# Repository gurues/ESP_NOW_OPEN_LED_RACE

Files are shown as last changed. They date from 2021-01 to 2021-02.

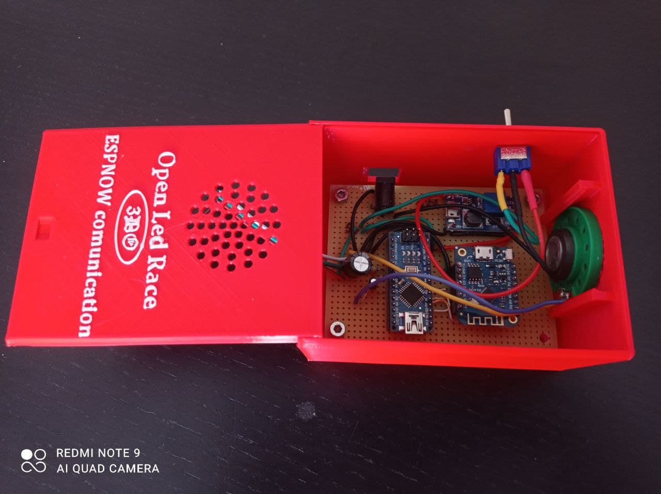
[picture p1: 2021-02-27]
Desing-3D/Fotos/Control_Box_7.jpg

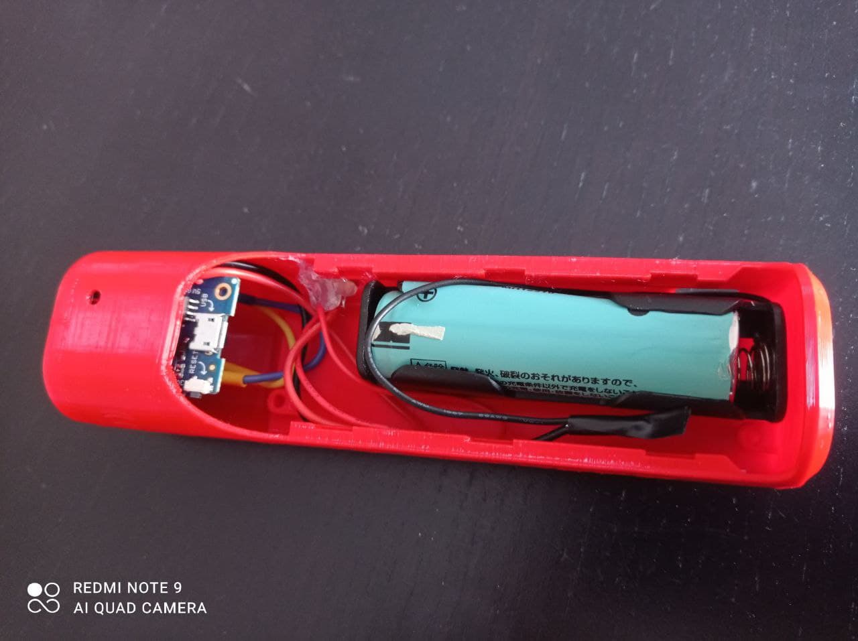
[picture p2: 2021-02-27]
Desing-3D/Fotos/OLR_Mando_Interior_4.jpg

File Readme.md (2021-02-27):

## -----------------------------------------------------------------------------------------------------------

# OPEN LED RACE ESPNOW COMUNICATION (4 PLAYER)

## ------------------------------------------------------------------------------------------------------------

### Cuando era pequeño siempre pedía para reyes un scalextri, pero los reyes pensaban en otros regalos mejores para mí

### Desde que vi el proyecto Open Led Race (https://openledrace.net/) sabía que lo construiría para mis hijos ... y para mí. Después ví un proyecto de Germán Martín realizando mandos inalámbricos mediante comunicación ESPNOW y ESP8266 (https://github.com/gmag11/OpenLedRace-Wireless-Remote). Investigue un poco sobre este tipo de comunicación (https://randomnerdtutorials.com/esp-now-many-to-one-esp8266-nodemcu/) y la aplique a este proyecto de una forma mucho más fácil y primitiva que Germán

### El resultado es una adaptación del código Open Led Race de 4 player (https://gitlab.com/open-led-race/olr-arduino) donde los mandos son inalámbricos mediante comunicación ESPNOW. He diseñado 2 pequeños códigos uno para los mandos con comunicación ESPNOW y otro para el Gateway ESPNOW

### El funcionamiento es muy básico, cuando se pulsa el pulsador de cualquier mando se produce una interrupción en el propio mando lo que provoca que se envíe un mensaje mediante el protocolo ESPNOW con la siguiente información:

- Número de Jugador
- Dato "0" o "1" (rota de forma cíclica -> 0, 1, 0, 1, 0 .......)
  
### El Gateway recibe todos los mensajes de los mandos enlazados al mismo, y teniendo en cuenta el Jugador y el dato asociado activa o no el puerto correspondiente al jugador en el Open Led Race

### Para que la comunicación entre los mandos y el Gateway ESPNOW sea efectiva es necesario saber la Mac Address del microcontrolador que realizará la función de Gateway, en nuestro caso un Wemos D1 mini. Para determinar la MAC puedes cargar el código que está en la carpeta "MAC_Address" en el Wemos del Gateway (código obtenido de https://randomtutorials.com/)

## MANDO ESPNOW

### El código de los mando con comunicación ESPNOW se encuentra en la carpeta "ESP_NOW_Mando_OLR"

### Para un funcionamiento correcto se debe modificar las siguientes variables:

### // Gateway_ESPNOW MAC Address

### uint8_t broadcastAddress[] = {0x??, 0x??, 0x??, 0x??, 0x??, 0x??};

- Introducir la dirección MAC del Gateway_ESPNOW para emparejar los mandos con el Gateway ESPNOW

### Indica el número del mando del jugador a configurar

### 1 -> Jugador 1   Rojo

### 2 -> Jugador 2   Verde

### 3 -> Jugador 3   Azul

### 4 -> Jugador 4   Blanco

### #define JUGADOR ?

- Introducir el número de jugador para que se configure dicho mando.

## GATEWAY ESPNOW

### El código del Gateway ESPNOW se encuentra en la carpeta "ESP_NOW_Gateway_OLR". No es necesaria la configuración de ninguna variable para su correcto funcionamiento

## OPEN LED RACE

### El código del programa Open Led Race se encuentra en la carpeta "Open_Led_Race_4_Player" y solo se ha modificado respecto al original lo siguiente:

- Aumentar la espera para la configuración de mandos y carrera
  - línea 825:   delay(3000);  // gurues -> Retraso para la configuración

- Configuración de 4 JUGADORES. Solo es necesario pulsar el último mando a configurar
  - linea 834:   controller_init( &switchs[2], DIGITAL_MODE, DIG_CONTROL_3 );  // gurues
  - linea 835:   car_init( &cars[2], &switchs[2], COLOR3 );                    // gurues
  - linea 836:   ++race.numcars;                                               // gurues

- Activación permanente del sonido
  - línea 866:   SMOTOR=1; // gurues -> Activación del sonido motor

### Si lo crees necesario, modifica los parámetros por defecto de la carrera. Se realiza en el archivo olr-param.h cambiando los siguientes parámetros:

- Número de led de la pista
  - línea 13:  #define MAXLED       300

- Número de led de los Boxes
  - línea 14:  #define BOXLEN       60

- Número de vueltas de la carrera
  - línea 15:  #define NUMLAP       5

### El Open Lace Race (4 Players) guarda las configuraciones en la EEPROM del Arduino nano, por lo que es posible que aún modificando el número de led en el programa si la EEPROM se ha actualizado no te actualice el número máximo de led. La modificación de los parámetros de configuración grabados en la EEPROM se pueden modificar mediante comandos por el puerto serie o con la aplicación desarrollada en el proyecto Open Lace Race (App -> https://gitlab.com/open-led-race/desktopapp/-/tree/master/). En la carpeta Desing-3D esta un manual para la configuración del Open Led Race mediante puerto serie en el archivo OLRN_Protocol_Serial.pdf

### La configuración de los jugadores y resto de opciones se mantienen como las del código original (https://openledrace.net/tutorials/), con la salvedad que para obtener un "0" o un "1" cuando se pulsa el mando es necesario observa el led del Wemos Gateway ESPNOW. Si el led está encendido el dato recibido es un "0" si está apagado el dato recibido es un "1". También cabe la posibilidad de añadir un led externo para verficar esta indicación conectándolo a la patilla D4 del Wemos Gateway ESPNOW, a través de una  resistencia de 220 ohmios. La modificación de los parámetros de configuración se ejecuta durante el proceso de arranque, cuando el dato recibido del mando correspondiente es un "0", igual que en el código original del Open Led Race. La única diferencia respecto a las configuraciones en el momento de arranque es que solo es necesario pulsar sobre el último mando a utilizar. Si quieres configurar para 3 Players, se pulsará el mando del Jugador 3 y si quieres configurar para 4 Players, se pulsará solo el mando del jugador 4

## INTERCONEXIÓN ENTRE OPEN LED RACE y GATEWAY ESPNOW / CONEXIONES MANDO ESPNOW OLR

### La conexión entre el Gateway ESPNOW y el Arduino Nano se realiza puerto a puerto: (WEMOS D1, D2, D3, D5) -> Arduino Nano (A2, A0, A3, A1)

### Las tiras de led pueden ser alimentadas a 5V o a 12V, por lo que en el diseño de las conexiones se incluye un interruptor para seleccionar la alimentación del proyecto, y de esta forma utilizar ambas tiras de led

### En la carpeta "Desing-3D" encontraras un esquema eléctrico de las conexiones realizadas así como su diseño PCB (El PCB no ha sido probado, por lo que no garantizo su funcionamiento). También encontraras una colección de fotos del proyecto

## CONEXIONES MANDO ESPNOW OLR

### Los mandos OLR ESPNOW se pueden realizar de tres formas diferentes:

- 1ª OPCIÓN: Mediante un porta baterias 18650 con cargador y protecciones inclidas en el "shield", botón pulsador y Wemos D1 mini.
- 2ª OPCIÓN: Mediante porta baterias 18650, modulo de carga y protecciones de baterias 18650 TP4056, microinterruptor de 2 polos, botón pulsador y Wemos D1 mini.
- 3ª OPCIÓN: Mediante botón puldador, "shield" porta baterias 18650, cargador y protecciones ademas de el WEMOS D1 mini o ESP32, todo en la misma placa. Esta opción es la más facil de montar y la más económica.

### En la carpeta "Desing-3D" encontraras fotos de las conexiones de los mandos OLR ESPNOW

## DISEÑOS 3D

### En la carpeta "Desing-3D" se encuentran los diseños 3D de los mandos ESPNOW, caja de control, soportes para los mandos y la caja de control así como soportes para la tira led

### El diseño de los mandos es de German Martín, con unas pequeñas modificaciones mias para ajustar dicho diseño a los componentes utilizados en este proyecto (Gracias Germán por compartir los diseños)

## MATERIAL NECESARIO

### Mandos y Gateway ESPNOW

- 5 Wemos D1 mini (4 mandos y el Gateway ESPNOW) (4,25 €) -> https://es.aliexpress.com/item/32529101036.html?spm=a2g0s.9042311.0.0.36f663c0WOJN3M
- 4 Pulsadores (5,69€) -> https://es.aliexpress.com/item/32858643564.html?spm=a2g0s.9042311.0.0.274263c0AGlmOz
- 4 Cargadores Batería 18650 (2,74€) -> https://es.aliexpress.com/item/32910602118.html?spm=a2g0s.9042311.0.0.274263c0Vn9AQd
- 4 WeMos D1 ESP-Wroom-02 ESP8266 Nodemcu con carga de batería 18650 (5,30 €) -> https://es.aliexpress.com/item/4000593916138.html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,scm-url:1007.13339.169870.0,pvid:7de114b2-5daf-4faa-872d-e3b3c1729299,tpp_buckets:668%230%23131923%2363_668%23888%233325%236_668%232846%238113%231998_668%232717%237561%23318_668%231000022185%231000066059%230_668%233468%2315608%23151
  (sustituye a 4 Wemos D1 mini y a los 4 cargadores 18650)
- 4 Wemos ESP-Wroom-32 Bateria-Wifi-Bluetooth (7,14 €) -> https://es.aliexpress.com/item/32819459737.html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,searchweb201602_,searchweb201603_
  (sustituye a 4 Wemos D1 mini y a los 4 cargadores 18650)
- 4 Baterías 18650 (14,95€) -> https://es.aliexpress.com/item/1005001969453906.html?spm=a2g0s.9042311.0.0.274263c08zAvmg
- 1 Adaptador de corriente Booster DC-DC 2A (1,50€) -> https://es.aliexpress.com/item/32952511309.html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,searchweb201602_,searchweb201603_
- 1 Conector de alimentación (2,01€) -> https://es.aliexpress.com/item/33026528272.html?spm=a2g0s.9042311.0.0.274263c0Vn9AQd
- 1 Interruptor de 3 posiciones (1,28€) -> https://es.aliexpress.com/item/32869900104.html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,searchweb201602_,searchweb201603_

### Open Led Race

- Tira de led de 5V o 12V 8112B (13,74 €) -> https://es.aliexpress.com/item/32682015405.html?spm=a2g0s.9042311.0.0.36f663c0WOJN3M
- 1 Ardino Nano Every (12,10 €) -> https://www.amazon.es/Arduino-Nano-Every-Single-Board/dp/B07VX7MX27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
- 1 Resistencia de 470 ohmios (1,64€) -> https://es.aliexpress.com/item/32317115890.html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,searchweb201602_,searchweb201603_
- 2 Condensadores electrolíticos de 1000 microfaradios (2,78€) -> https://es.aliexpress.com/item/32954075821.html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,searchweb201602_,searchweb201603_
- 1 Condensador electrolítico de 1 microfaradio (4,84€) -> https://es.aliexpress.com/item/4000020803391.html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,searchweb201602_,searchweb201603_
- 1 Altavoz 8R 0.25W 40 mm (1,58€) -> https://es.aliexpress.com/item/4001098796204.html?spm=a2g0s.9042311.0.0.274263c0AGlmOz
- Fuente alimentación 5V 3A (4€) -> https://es.aliexpress.com/item/32986101102.html?spm=a2g0s.9042311.0.0.274263c0AGlmOz

## -----------------------------------------------------------------------------------------------------------

# OPEN LED RACE ESPNOW COMUNICATION (2 PLAYER)
## -----------------------------------------------------------------------------------------------------------

### En la carpeta "ESP_NOW_Gateway_OLR_2P" se dispone del código Open Led Race, versión Arduino-Basico (https://gitlab.com/open-led-race/olr-arduino-basic), adaptado para que mediante solo el Gateway ESPNOW poder controlar la tira de led. Resumiendo, eliminando el Arduino Nano y manteniendo el resto de componentes disponenos de un Open Led Race para 2 jugadores (necesario 3 Wemos y el resto de componentes)

### Creo que la versión de 4 player también es posible realizar esta modificación pero es bastante más complicada por lo que ya veré si lo intento más adelante

## -----------------------------------------------------------------------------------------------------------

# PLATFORMIO

## -----------------------------------------------------------------------------------------------------------

### El proyecto está realizado con Platformio y para cargar el código en los respectivos microcontroladores será necesario ejecutar los siguientes instrucciones

### 1.- Abrir un terminar Platformio

### 2.- Desplázate a la carpeta del código que quieras cargar (ESP_NOW_Gateway_OLR, ESP_NOW_Mando_OLR, etc)

### 3.- Ejecuta la siguiente instrucción para cargar el código en un Wemos d1 mini (Gateway ESPNOW o Mando)

            pio run -e d1_mini -t upload 

### 4.- Ejecuta la siguiente instrucción para cargar el código en un ESP32 esp-wroom-32 (Mando)

            pio run -e wemosbat -t upload 

### 5.- Ejecuta la siguiente instrucción para cargar el código en un Arduino Nano (Open Led Race - Pistas máximo 300 led)

            pio run -e nano328 -t upload

### 6.- Ejecuta la siguiente instrucción para cargar el código en un Arduino Nano Every (Open Led Race - Pistas máximo 1500 led)

            pio run -e nano_every -t upload 

### 7.- Si quieres activar el monitor serie, ejecuta a continuación

            pio device monitor -b 115200

## -----------------------------------------------------------------------------------------------------------

# PRESUPUESTO
## -----------------------------------------------------------------------------------------------------------

### Por unos 80€ puedes disponer de un Open Led Race con Arduino Nano Every, tira de led de 5 metros (60 led/metro IP67) y 4 mandos inalámbricos ESPNOW

### Por unos 40€ puedes disponer de un Open Led Race Wemos Gateway ESPNOW, tira de led de 5 metros (60 led/metro IP67) y 2 mandos inalmbricos ESPNOW

## -----------------------------------------------------------------------------------------------------------

# AGRADECIMIENTOS
## -----------------------------------------------------------------------------------------------------------

### Quiero agradecer a los creadores del proyecto Open Led Race su gran trabajo e imaginación para darnos la posibilidad de disfrutar de este proyecto (https://openledrace.net/)

## También quiero agradecer:

- A Germán Martín su paciencia con las preguntas "nóveles" que tuvo el placer de contestarme en los inicios de este proyecto, así como su aportación "al mundo maiker" compartiendo un gran número de proyectos y librerías (https://github.com/gmag11)
- A Rui Santos por sus grandísimos tutoriales de los cuales he aprendido para poder realizar este y otros proyectos (https://randomtutorials.com/)

## gurues@2021

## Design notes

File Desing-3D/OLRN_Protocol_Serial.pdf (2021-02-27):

# OLR Serial Protocol (Board←→Host)

### Table of Contents

Open LED Race - Serial Protocol Ver 1.0 | Pag: 1/24 | Revision: 2020-12-07

## Terminology

In the present doc the terms Board and Host indicate:
- Board: OLR Board - The microcontroller managing the led strip (Arduino)
- Host: A Software running on a computer connected to the Board via Serial interface (Currently only USB).
The software can be “OLR Update/Configuration Utility”, “OpenLEDRace Network Client”, etc.

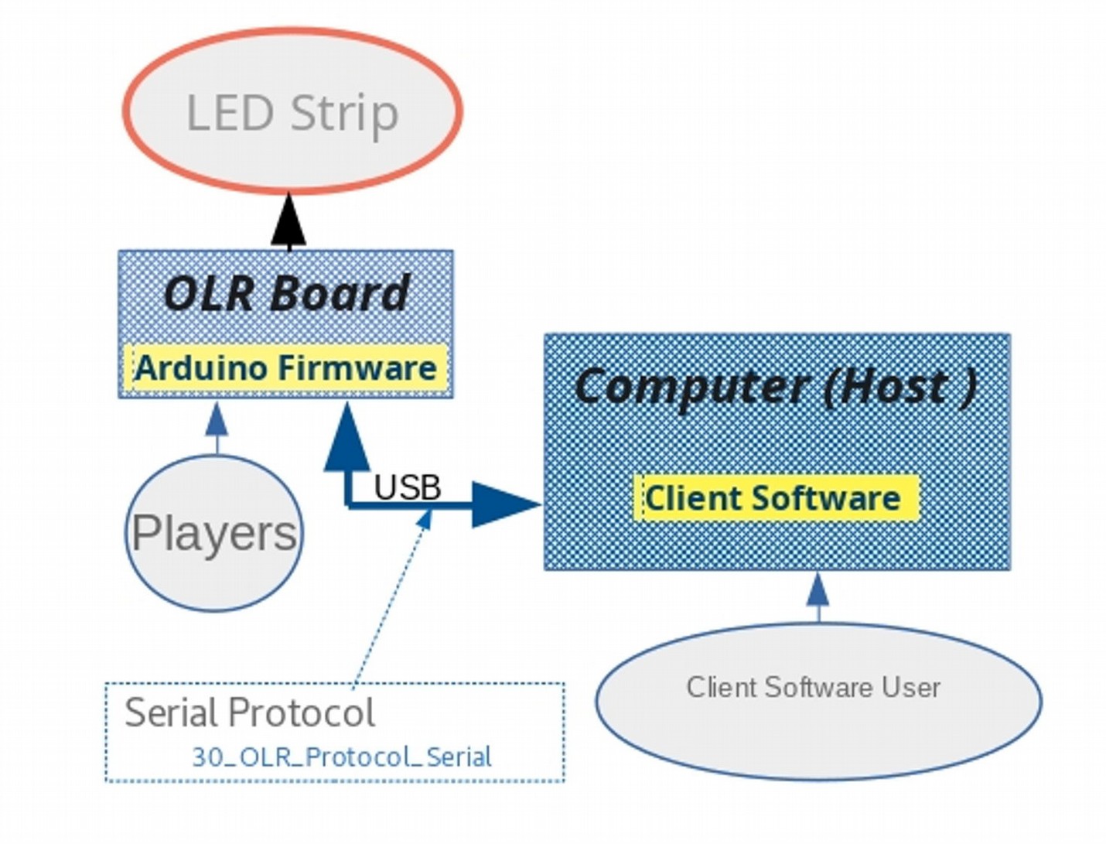
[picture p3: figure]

The software running on Host and the Firmware on Board communicate using the Protocol described in the present document.

## Implementation notes

Message format

Messages are “arrays of chars” composed by:
- Command_id: one char identifying the command, case sensitive
- Optional Parameters (not every command have parameters)
- If a command have parameters, the first one comes immediatly after the command_id (no separators).
- In case command have more than one parameter, the following ones are comma-separated
- EOC - End Of Command char:
- ASCII 10/0x0A = Line Feed = new line = ‘\n’
- Example: C1,3,1,1\n
- Command “C” (race configuration) with parameters, ended with the EOC character
Open LED Race - Serial Protocol Ver 1.0 | Pag: 2/24 | Revision: 2020-12-07

## Commands List

Cmd | | Description | Notes
| # Protocol Handshaking Host-Board handshake on startup
| @ Enter Configuration mode Host request the Board to enter in configuration mode
| ~ Leave Configuration mode Host request the Board to leave configuration mode
| : Set Unique ID Set Board Unique ID
| $ Get UID Get Board Unique Id
| ? Get Software Id (Type) Get Board Software Type (OLR, OLRNet,...) --see specific doc with defined SoftwareType IDs
| % Get Software Version Get Board software version
| ! Send log/error msg Send a log/error message to peer
| C Race Configuration Set main race configuration parameters
| T Track length configuration Command used to configure the Total Number of LEDs in the track.
| B Box length configuration Command used to configure the PitLane (Box)
| A Ramp (Slope) configuration Command used to configure the Ramp (Hill, Slope)
| K Physics parameters configuration Configure “Weight” and “Friction” constants
| H OutTunnel distance notification Set the positions where Board will send the notification for a Car reaching the OutTunnel (The car is ‘n’ position away from the OutTunnel)
| D Load Racetrack defaults Reset to defaults the Racetrack configurable parameters (Track length, Box length, etc)
| W Save current configuration Tell the Board to permamently store current configuration
| Q Query board cfg Host request the current situation of the Config Parameters Set
| R Race phase Command used to notify current Race phase
| p Car current position Telemetry: Car current position in the Racetrack
| r Car Leaving Car is ‘n’ position away from the OutTunnel. The next OLR in the race (the one receiving the car) will receive a ‘Car Coming’ command.
| s Car Left Car is in the last position before OutTunnel. The next OLR in the race will receive a ‘Car Arrived’ command.
| t Car Coming A car is arriving in the OLR (The circuit where it’s now sent a ‘Car Leaving’ command). The Players will see the InTunnel turned on with the color of the arriving car
| u Car Enter A car enter the OLR (The circuit where the car was until now sent a ‘Car Left’ command). The car will ‘come out’ here from the inTunnel.
Open LED Race - Serial Protocol Ver 1.0 | Pag: 3/24 | Revision: 2020-12-07

Cmd | Description | Notes
w Car Win the Race | A car just won the current race

## Commands Description

In the following sections the column “Initiate“ contains the id of the board sending the message.
- B - Board: OLR Board (Arduino Nano)
- H - Host: Host where the OpenLedRace Network Client is running (Computer).
Same rule applies to the “From“ column in “Response“
Some commands may be originated by both peers (ex: Handshake, racephase, etc)
The string [EOC] indicates the EOC (End of Command) char = “line feed” = ASCII 10 (0A)

# protocol handshaking

# | Protocol Handshaking

Initiate | Syntax | Description
B, H | #[EOC] | Sent to initialize a connection (Board and Host)
Response | From | Notes
#[EOC] | H, B | The connection opens succesfully when a “#” is received ‘back’ from the peer

@ Enter Configuration mode

@ | Enter Configuration mode request
initiate | Syntax | Description
H | @[EOC] | Sent from Host to put the board in configuration mode. The OLR Board wil stop managing the current status and wait for configuration commands
Response | From | Notes
@OK[EOC] | B | Board sends “OK” string
@NOK[EOC] | B | Board indicates something went wrong
Open LED Race - Serial Protocol Ver 1.0 | Pag: 4/24 | Revision: 2020-12-07

~ Leave Configuration mode

~ | Leave Configuration mode request
initiate | Syntax | Description
H | ~[EOC] | Sent from Host to tell Board to leave the “Configuration mode” and goes to the “running” status (firmware-dependent)
Response | From | Notes
~OK[EOC] | B | Board sends “OK” string
~NOK[EOC] | B | Board indicates something went wrong
: | set board id

Not every OLR Board have a unique ID stored in EEPROM.
Currentrly only “Open LED Race Network” game (Network client and firmware) uses the UID.

The Host uses the Set Board Unique Id command to permanently store and UID into the board’s EEPROM.
The Board writes the ID to EEPROM immediately (no “B” command needed after “:”)
: | Set board Unique Id
initiate | Syntax | Description
H | :id[EOC] | Set Board Unique Id request Sent from Host to Set Board’s Unique Id

Parameter
Id | See “UID_format” below | String representing the Unique Id.
Response | From | Notes
:OK[EOC] | B | Board sends “OK” string
:NOK[EOC] | B | Board indicates something went wrong

Unique Board Id (UID) string format:
^[\x33-\x7E]{16}$
Lenght: 16 chars
Valid Chars: Ascii 7-bit Printable Chars excluding ‘space’=ASCII 32 (this means ASCII chars
| between 33 (0x21) and 126 (0x7E) inclusive
Open LED Race - Serial Protocol Ver 1.0 | Pag: 5/24 | Revision: 2020-12-07

$ | get board id
$ | Get Board Id
initiate | Syntax | Description
H | $[EOC] | Get Board Id request Sent from Host to get Board’s Unique Id
Response | From | Notes
$Id[EOC] | B | Send the UID strings

Examples

Origin | Command | Description
H | $[EOC] | Host send a get BoardId request
B | $3179c3ec6e28ah64[EOC] | The Board send back the UID (3179c3ec6e28ah64)
Origin | Command | Description
H | $[EOC] | Host send a get info request
B | $?????????[EOC] | The Board send back an invalid UID (if you are looking at it in a Serial Console, you usually see a bunch of question marks or other chars / non-printable ASCII). This usually happens when the UID is not set yet, so the Board send back the contents of the area of the EEPROM where the UID is supposed to be stored.
Open LED Race - Serial Protocol Ver 1.0 | Pag: 6/24 | Revision: 2020-12-07

? get software type ID

Used to identify the software installed on the Board

? | Get Software Type Id
initiate | Syntax | Description
H | ?[EOC] | OLR Board software Id request
Response | From | Notes
?ver[LF] | B | Where “ver” is the string representing the Software Id

Software Id String format

[0-9a-zA-Z]+.[0-9a-zA-Z]+.[0-9a-zA-Z]+.[0-9a-zA-Z]+ Four numbers and/or letters.

Example

Origin | Command | Description
H | ?[EOC] | Host send a get software id request
B | ?A4P0[EOC] | The message from the Board indicates ID="A4P0"

Guidelines to Assign a software Id to the Arduino Software:

The fist char represents the main category:
- "A" - Open LED Race, developed by Open LED Race Team
The next theree chars identify the software itself:
- 4P0 : 4 Players with Pitlane and Slope (our standard 4 players software)
- 2N0 : Open LED Race Network 2 players
Open LED Race - Serial Protocol Ver 1.0 | Pag: 7/24 | Revision: 2020-12-07

% get software version

Used by Host to check software compatibility with Board’s software version

% | Get Software Version
initiate | Syntax | Description
H | % [EOC] | OLR Board software version request
Response | From | Notes
%ver[LF] | B | Where “ver” is the string representing the Software Version

Software Version String format

[0-9]+\.[0-9]+\.[0-9]+
Three dot-separated decimal numbers.

Example

Origin | Command | Description
H | %[EOC] | Host send a get software version request
B | %0.8.1[EOC] | The message from the Board indicates Version=”0.8.1”

Version Number Guidelines
The three numbers represents the “Major.Minor.Patch” version.

Guidelines to Assign a version number to the Arduino Software:
- Major version zero (0.y.z) is for initial development. Anything MAY change at any time.
- Version 1.0.0 defines first ‘Stable’ version
- Increment:
- MAJOR version when you make incompatible changes
- MINOR version when you add functionality in a backwards compatible manner
- PATCH version when you make backwards compatible bug fixes.
Open LED Race - Serial Protocol Ver 1.0 | Pag: 8/24 | Revision: 2020-12-07

! send log/error message
The software running on the Board use this command to send messages to be written into the Host logfile.
The Host will log the message and decide what to do with the relay race according to the “Type” parameter (do nothing, stop the race, etc.)
! | Send log/error message
initiate | Syntax | Description
B | !Type,Message[EOC] | Board sends an error/log message to Host

Parameters
Type | [0-3] | single char
| 1 | Log only - Board want to write a log a message into the Host’s LogFile, Sent usually in development/debug phase to trace the dialog between Board and Host
| 2 | Warning - Board send back a “warning” message Sent by board on ‘not blocking’ errors like, for example, unknown commands or parameters
| 3 | Blocking Error - The boards have a Severe error condition and cannot proceed. The Host will log the message into the Host Message LogFile and decide what to do (if the Host is running a RelayRace it will Stop the Race)
Message | String | Message Board want to write into the Host’s LogFile
Response | From | Notes
| H | No answer sent from Host

Example

Origin | Command | Description
B | !1,invalid Car=[3] in [t] command [EOC] | Board send a warning message about a previously received command
Open LED Race - Serial Protocol Ver 1.0 | Pag: 9/24 | Revision: 2020-12-07

C set race Configuration

C | Set Race Configuration Parameters
initiate | Syntax | Description
H | Cstart,nlap,repeat,finish[EOC] | Host Send Race configuration parameters to Board
Parameter Format | | Description
start | [0-1] | OLR Network: Start Line of the race is in this Board ? (Y/N) (0=No, 1=Yes) OLR Standalone: Always 1 for standalone OLR
nlap | [1-9][0-9]? max 2 chars (range 1-99) | OLR Network: Number of consecutive laps in each section of the Relay Race (consecutive laps the cars will “run” before race finish or car get trough the OutTunnel) OLR Standalone: Number of laps of a Race
repeat | [1-9][0-9]? max 2 chars (range 1-99) | OLR Network: Number of times to repeat the configured section of ‘nlap’ laps OLR Standalone: Always 1 for standalone OLR
finish | [0-1] | OLR Network: Finish Line of the race is in this Board ? (Y/N) (0=No, 1=Yes) OLR Standalone: Always 1 for standalone OLR
Response | From
COK[EOC] | B | Board sends “OK” string
CNOK[EOC] | B | Board indicates that something went wrong (ex: wrong parameter value or format)
Open LED Race - Serial Protocol Ver 1.0 | Pag: 10/24 | Revision: 2020-12-07

Set Race Configuration Examples

Example 1 | OLR Network
Origin | Command | Description
H | C0,5,2,1[EOC] | start=0: The Race starts in another OLR – The Board will be waiting for messages like “Race Started”, “Car 1 Leaving”, Car 1 Left”, etc…
| | laps=5: Each car will need to complete 5 laps before it can cross the Finish Line or get to the next OLR (see ‘repeat’ param)
| | repeat=2: Each car will need to repoeat 2 times the section of ‘nlap’ laps. This means we’ll expect each car will be sent back here after we previously sent it out to another Racetrack.
| | finish=1: The Race ends here.This OLR will manage the Finsh Line Procedure.
B | COK[EOC] | Response from the Board. Values for Position,Laps,Repeat,Finish has been set as requested by the host.
Example 2 | OLR Network
Origin | Command | Description
H | C1,2,3,0[EOC] | start=1: The Race starts here (This Board will be managing the Start Race phase – Semaphore countdown, etc.)
| | laps=2: Each car will need to complete 2 laps before can get to the next Racetrack
| | Repeat=3: Each car will need to repeat 3 times the section of ‘nlap’ laps.
| | finish=0: The Race ends in another OLR.
B | COK[EOC] | Response from the Board. Values for Position,Laps,Repeat,Finish has been set as requested by the host.
Example 2 | OLR Standalone
Origin | Command | Description
H | C1,3,1,1[EOC] | laps=3: Each car will need to complete 3 laps before it can cross the Finish Line
B | COK[EOC] | Response from the Board – Race Configured OK
Open LED Race - Serial Protocol Ver 1.0 | Pag: 11/24 | Revision: 2020-12-07

T Track configuration – Total LEDs Number

T | Pit Lane (Box) configuration
initiate | Syntax | Description
H | Tnled[EOC] | Host Set Racetrack Length Configuration
Parameter | Format | Description
nled | Total number of LEDs in the Track | Ex: 300 for a single 5mt - 60 LED/mt LED Strip
Response | From | Notes
TOK[LF] | B | Board sends “OK” string
TNOK[LF] | B | Board indicates that something went wrong

Example

Origin | Command | Description
H | T600[EOC] | Total Length is 600 (2 x 300 LED Strip connected).
B | TOK[EOC] | Response from the Board: the value for “Racetrack Length” has been set

Note:
Usually, after sending this command, the board have to be hard-reset to re-initate the library managing the LED strip (firmware allocates space for the LED array in the setup() function)
Open LED Race - Serial Protocol Ver 1.0 | Pag: 12/24 | Revision: 2020-12-07

B Track configuration – Pitlane length (Boxes)

B | Pit Lane (Box) configuration
initiate | Syntax | Description
H | Bnled,perm[EOC] | Host request the Board to Set the Pitlane length to a specific value
Parameter | Format | Description
nled | [0-MAXLED] | Total number of LEDs, at the end of the Racetrack, reserved for the Pitlane
perm | [0-1] | Box always on? (Y/N) • [0] to activate Pitlane players have to push the Activate Pitlane button on Startup (default behaviour) • [1] the board will always activate pitlane on startup.
Response | From | Notes
BOK[LF] | B | Board sends “OK” string
BNOK[LF] | B | Board indicates that something went wrong

Example

Origin | Command | Description
H | B120,0[EOC] | Total Length for Pitlane is 120 LEDs, perm=0 → default behaviour, the board will do not activate pitlane unless user push “Activate Pitlane” button on startup
B | BOK[EOC] | Response from the Board: the value for “Pitlane Length” has been set
Open LED Race - Serial Protocol Ver 1.0 | Pag: 13/24 | Revision: 2020-12-07

A Track configuration – Ramp configuration

A | Ramp (Slope) configuration
initiate | Syntax | Description
H | Astart,center,end, high,perm[EOC] | Host set the Ramp configuration
Parameter | Format | Description
start | | LED number where the ramp Starts
center | | LED Number where ramp is centered.
end | | LED number where the ramp ends
height | [ 0 - 1023] | Ramp elevation
perm | [0-1] | Ramp always on? (Y/N) • [0] to activate Ramp/Slope players have to push the Activate Ramp button on Startup (default behaviour) • [1] the board will always activate Ramp/Slope on startup.
Response | From | Notes
AOK[EOC] | B | Board sends “OK” string
ANOK[EOC] | B | Board indicates that something went wrong

Example

Origin | Command | Description
H | A140,150,160,12,0[EOC] | Set the ramp centered in led 150 with an elevation of 12, perm=0 → default behaviour, the board will do not activate slope unless user push “Activate Slope” button on startup
B | AOK[EOC] | Response from the Board: values for “Slope” has been set
Open LED Race - Serial Protocol Ver 1.0 | Pag: 14/24 | Revision: 2020-12-07

K Track configuration – Physics configuration

K | Weight, Friction configuration
initiate | Syntax | Description
H | Kkg,kf[EOC] | Weight and Friction constants configuration
Parameter | Format | Description
kg | [0-1]+\.\d{3} Range: 0.0001–1.999 | Weight constant: Used to calculate speed loss/gain on slopes
kf | [0-1]+\.\d{3} Range: 0.0001–1.999 | Frictions constant: Used to calculate speed loss when player does not push the controller
Response | From | Notes
KOK[EOC] | B | Board sends “OK” string
KNOK[EOC] | B | Board indicates that something went wrong

Example

Origin | Command | Description
H | K0.006,0.015[EOC] | Set weight constant to 0.006 and Friction to 0.015
B | KOK[EOC] | Response from the Board: values for kg, kf has been set
Open LED Race - Serial Protocol Ver 1.0 | Pag: 15/24 | Revision: 2020-12-07

H out tunnel distance notification (OLR Network only)

N | Set ‘car is Reaching the OutTunnel’ notification distance
initiate | Syntax | Description
H | Hnum[EOC] | Set the positions where the Board will send the notification message for a Car reaching the OutTunnel (the car is num position away from the OutTunnel). It will be used by the “next” board in the relay race to ‘light up’ its input tunnel visual effect
Parameter | Format | Description
num | [0-9]+ | One or more char representing a decimal number
Response | From | Notes
NOK[LF] | B | Board sends “OK” string
NNOK[LF] | B | Board indicates that something went wrong

Example

Origin | Command | Description
H | H8[EOC] | Host request the board to set the Reaching tunnel nofication distance to ‘8’
B | HOK[EOC] | Response from the Board: the value for “Notification distance” has been set
Open LED Race - Serial Protocol Ver 1.0 | Pag: 16/24 | Revision: 2020-12-07

D reset basic params to Default values
Reset to the program-defined default values any configurable parameter.
- Ramp (Slope)
- Pit Lane (Box)
- LED number (strip length)
- Race laps number
- Friction/Gravity Constant
D | Reset params to default values as defined in the source file
initiate | Syntax | Description
H | D[EOC] | Host request a Reset to Default configuration
Response | From | Notes
DOK[EOC] | B | Board sends “OK” string (ACK)
DNOK[EOC] | B | Board indicates that something went wrong

W Writes current parameter set to EEPROM
After changing values in the parameter set the Host calls this commad to store permanently the new configuration.
D | Reset params to default values as defined in the source file
initiate | Syntax | Description
H | W[EOC] | Host request to save current parameter set to EEPROM
Response | From | Notes
WOK[EOC] | B | Board sends “OK” string (ACK)
WNOK[EOC] | B | Board indicates that something went wrong
Open LED Race - Serial Protocol Ver 1.0 | Pag: 17/24 | Revision: 2020-12-07

Q Query current parameters set

Q | Current paremeters values stored on the Board
initiate | Syntax | Description
H | Q[EOC] | Host request the current configurable parameters values
Response | From | Notes
TRACK:a,b,c,d,e,f,g,h[EOC] RAMP:a,b,c,d[EOC] RACE:a,b,c,d[EOC] | B | Board issue 3 messages (3 x [EOC]) containing the whole set of configurable values

Returned parameters description

Track params
a | nled_total | Total number of LEDs in the Racetrack (configurable with "T" command)
b | nled_main | debug parameter: when Pitlane is active: number of LEDs currently in the Main Path
c | nled_aux | debug parameter: when Pitlane is active: number of LEDs currently in the Pitlane Path
d | nled_init_aux | debug parameter: position of the Pitlane entrance
e | box_len | Total number of LEDs, at the end of the Racetrack, reserved for the Pitlane (configurable with "B" command)
f | box_alwaysOn | the board always activate pitlane on startup [0|1] (configurable with "B" command)
g | weight_const | Weight constant: Used to calculate speed loss/gain on slopes
h | friction_const | Frictions constant: Used to calculate speed loss when player does not push the controller

Ramp params
| start | LED number where the ramp Starts
| center | LED Number where ramp is centered.
| end | LED number where the ramp ends
| height | Ramp elevation
| alwaysOn | the board always activate Ramp/Slope on startup [0|1]
Race params
| start | OLRNetwork Only - Always 1 for standalone OLR
| nlap | Number of laps of a Race (Configurable with 2nd parameter of "C" Command)
| repeat | OLRNetwork Only - Always 1 for standalone OLR
| finish | OLRNetwork Only - Always 1 for standalone OLR

Example
Origin | Command | Description
H | Q[EOC] | Host send a get current paremeters Set request
B | TRACK:1200,1200,0,-1,60,0,0.006,0.015[EOC] RAMP:180,190,200,15[[EOC] RACE:1,2,1,1[EOC] | Messages from the Board with the current cfg values
Open LED Race - Serial Protocol Ver 1.0 | Pag: 18/24 | Revision: 2020-12-07

R Race phase

R | Current Race Phase
initiate | Syntax | Description
B,H | Rnum[EOC] | Current Race phase Board and Host send this command to notyfy changes in Race Status
Parameter | Format | Description
num | [0-9] | single numeric char
Initiate | Value | Description
B | 0 | Idle
H | 1 | Host request the Board to enter in configuration mode --DEPRECATED-- Use the “@” command
B | 2 | Configuration Complete. Board send this after receiving the last needed configuration parameter
H | 3 | Race Ready Sent from Host when every participant Board reach the [Configuration Complete] status When the OLR where Race starts receive this, it starts the Countdown
B,H | 4 | Countdown started (Red light on) The OLR where race starts send this message - any other OLR in the same Race will receive it
B,H | 5 | Racing - Race Started (Countdown finished) The OLR where race starts send this message and any other participant OLR will receive it
B,H | 6 | Race Paused (Safety car) not implemented
B,H | 7 | Resume Race (Safety car leave) not implemented
B,H | 8 | Race Complete The OLR managing the Finish line send this message when the winner cross it. Any other participant OLR will receive the message
Response | From | Notes
ROK[LF] | B | Board sends “OK” string
RNOK[LF] | B | Board indicates that something went wrong

Example
Origin | Command | Description
B | R4[EOC] | Board send this when the Countdown phase starts.
Open LED Race - Serial Protocol Ver 1.0 | Pag: 19/24 | Revision: 2020-12-07

p Telemetry: current car Position in race

p | Position for each car in the race
initiate | Syntax | Description
B | pCnumStrackNlap,Rpos[EOC] | Position for each car in the race Sent during race for each car currently in this Board.
Parameter | Format | Description
Cnum | [1-9] | One char representing Car Number
Strack | [A-Z] | One char representing the SubTrack where the car is
| M | Main Track
| B | Box Track (Pit Lane)
| U | Not a Track
Nlap | [1-99] | Number of the Current Lap.
Rpos | [00-99] | Relative position in a track (percentage)
Response | From | Notes
| H | No response from host

Example

Origin | Command | Description
B | p1B1.95p2M5.45[EOC] | • Two cars are currentry "running" in the Board: ◦ Car "1" is in Track "B" in Lap number "1", relative Lap Position 95% ◦ Car "2" is in Track "M" in Lap number "5", relative Lap Position 45%
Open LED Race - Serial Protocol Ver 1.0 | Pag: 20/24 | Revision: 2020-12-07

r | Car leaving (OLR Network only)
r | Car is about to leave the current Racetrack
Initiate | Syntax | Description
B | rNum[EOC] | Car ‘Num’ is ‘n’ position avay from OutTunnel Sent during race so the next OLR in the race (the one receiving the car) will turn on the InTunnel light effects.The Playere will sees the InTunnel turned on with the color of the arriving car
Parameter | Format | Description
Num | [1-9] | One char representing Car Number
Response | From | Notes
| H | No response from host

Example
Origin | Command | Description
B | r1[EOC] | Car “1” reached the distance from tunnel specified with the ‘N’ config param
s | Car left the circuit - last position reached (OLR Network only)
s | Car left
initiate | Syntax | Description
B | sData[EOC] | Car is at the last valid position of the path ‘Data’ byte contains car id and speed
Parameter | Format | Description
Data | Byte (char) | One byte representing Car Number and speed
| Speed → Bits:[0:4] | 5 bits representing speed
| Car Num → Bits:[5:7] | 3 bits representing the car number
Response | From | Notes
| H | No response from host

Example
Origin | Command | Description
B | s00100100[EOC] | Please note: 00100100 is not the “00100100” string !!! It represents the binary value of one byte: Bits:[0:4] = 00100 Bin representation Dec “4” → Bin representation Dec “4” Bits:[5:7] = 001 Bin representation of Dec “1” → Bin representation Dec “4” Car “1” Laved the Racetrack with speed ‘4’ If you look at this command in a Serial console, you will see “s$” (ASCII table: dec:36 Binary:00100100 Char:$ → Bin representation Dec “4” → Bin representation Dec “4” )
Open LED Race - Serial Protocol Ver 1.0 | Pag: 21/24 | Revision: 2020-12-07

t | Car coming (OLR Network only)
r | Car is about to enter into the Racetrack
Initiate | Syntax | Description
H | tNum[EOC] | Car ‘Num’ is arriving. Received during the race when a car is arriving from another OLR. This Board will turn the InTunnel On
Parameter | Format | Description
Num | [1-9] | One char representing Car Number
Response | From | Notes
| B | No response from Board

Example
Origin | Command | Description
H | t1[EOC] | Car “1” is ‘n’ step away from here….
u | Car enter the circuit (OLR Network only)
u | Car arrived to this Racetrack
initiate | Syntax | Description
H | uData[EOC] | Car ‘Num’ with ‘Speed’ enters the circuit ‘Data’ byte contains car id and speed Received during the race when a car arrives from another OLR.
Parameter | Format | Description
Data | Byte (char) | One byte representing Car Number and speed
| Speed → Bits:[0:4] | 5 bits representing speed
| Car Num → Bits:[5:7] | 3 bits representing the car number
Response | From | Notes
| B | No response from Board

Example
Origin | Command | Description
B | u00100100[EOC] | Car “1” Laved the Racetrack with speed ‘4’ – see description in command “s”–Car Left example
Open LED Race - Serial Protocol Ver 1.0 | Pag: 22/24 | Revision: 2020-12-07

w Car win the race

w | Car win the current race
Initiate | Syntax | Description
B | wNum[EOC] | Car ‘Num’ just win the race Sent by the Board when a car cross the Finish Line
Parameter | Format | Description
Num | [1-9] | One char representing Car Number
Response | From | Notes
| H | No response from Host

Example
Origin | Command | Description
B | w1[EOC] | Car “1” won the race
Open LED Race - Serial Protocol Ver 1.0 | Pag: 23/24 | Revision: 2020-12-07

## Document revisions:

- 2020_12_07: Luca – Ver 1.0
- Changed ID for command “Boxlength (from “T” to “B”)
- Added command:
- @ - Enter Configuration mode (R1 is now deprecated)
- ~ - Leave Configuration mode
- K – Physics constants configuration (kf, kg)
- T - Track length configuration (number of LED in racetrack)
- ? - Get Software Type
- W – Write / store permanently current parameter (ex: EEPROM)
- 2020_04_24: Luca
- Modified “Get Software Version→Version StringFormat”
- Doc cleanup
- 2019_09_15: Angel
- Added T,A and D commands
- 2019_08_31: Angel
- Modified u and s command to include car speed
- 2019_08_04: Angel
- Modified [Get UID] command
- 2019_08_03: Angel
- Changed field separator character to “,”
- Review command [Race Phase]
- 2019_07_30: Luca
- added [get Software Version] command
- modified [get board info] -> [get Board UID]
- 2019_07_29: Angel
- added commands [Configuration Race ]
- deleted commands [Race Starts here ] [Laps number ] [Repeat Section number ] [Race Finish Line ]
- 2019_07_27: Luca
- added commands [Car Arriving] [Car Arrived] with ‘Special’ command format
- added commands [Send Log/Error] [Car Win] [Query Board cfg]
- added parameter values to [Race Phase] command
- modified parameter [P] from Position[0-9]+ to StartsHere[0-1]
- deleted [Car current lap] parameter (not used)
- 2019_07_15: Luca
- added commands [Reset][Get Board Info] [Set Unique Id]
- 2019_05_10: Angel
- added commands [Car Current Position]
- 2019 march
- Doc created
Open LED Race - Serial Protocol Ver 1.0 | Pag: 24/24 | Revision: 2020-12-07

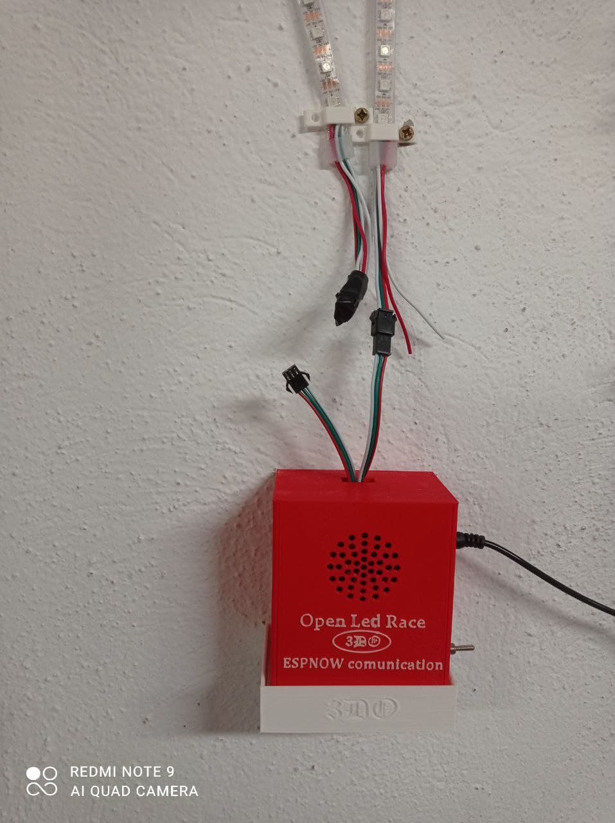
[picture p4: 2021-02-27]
Desing-3D/Fotos/Control_Box_2.jpg

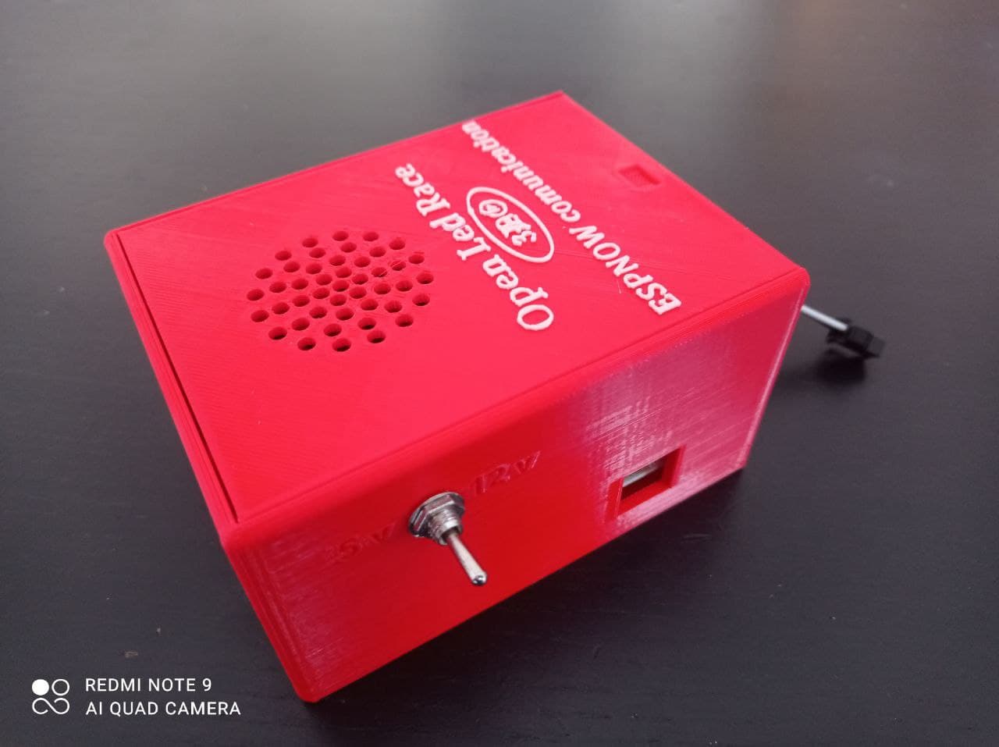
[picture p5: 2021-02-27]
Desing-3D/Fotos/Control_Box_3.jpg

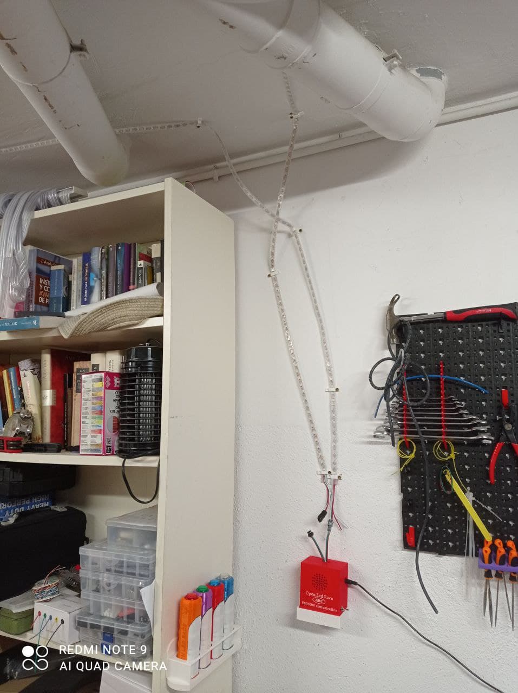
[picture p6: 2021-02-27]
Desing-3D/Fotos/OLR_ESP_NOW.jpg

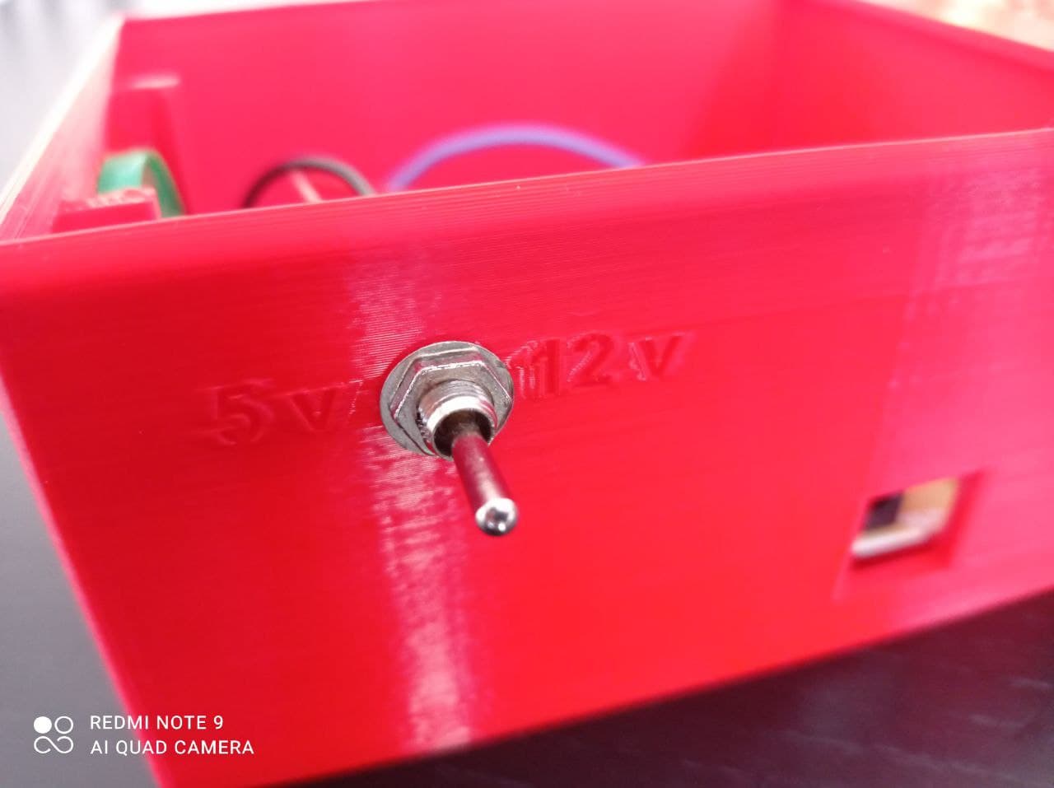
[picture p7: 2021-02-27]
Desing-3D/Fotos/Control_Box_6.jpg

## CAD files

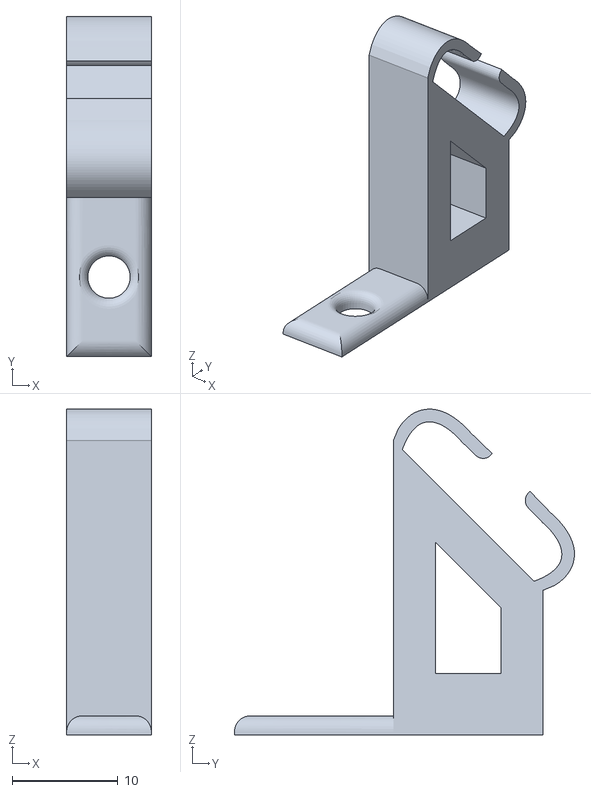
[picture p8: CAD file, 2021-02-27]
Desing-3D/3D/Sujeccion_Led_45.stl
8.00 x 32.1 x 30.8

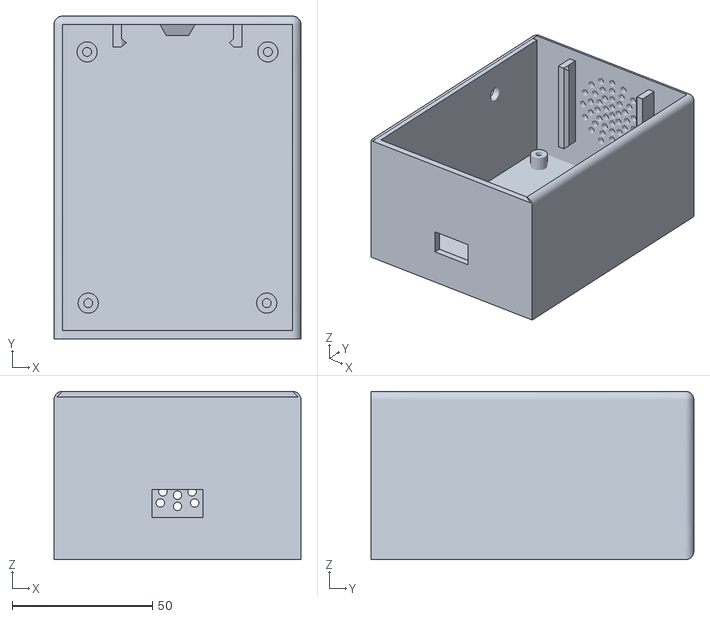
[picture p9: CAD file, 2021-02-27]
Desing-3D/3D/OLR_Box_Control-Gateway_2.stl
88.0 x 115.0 x 60.0

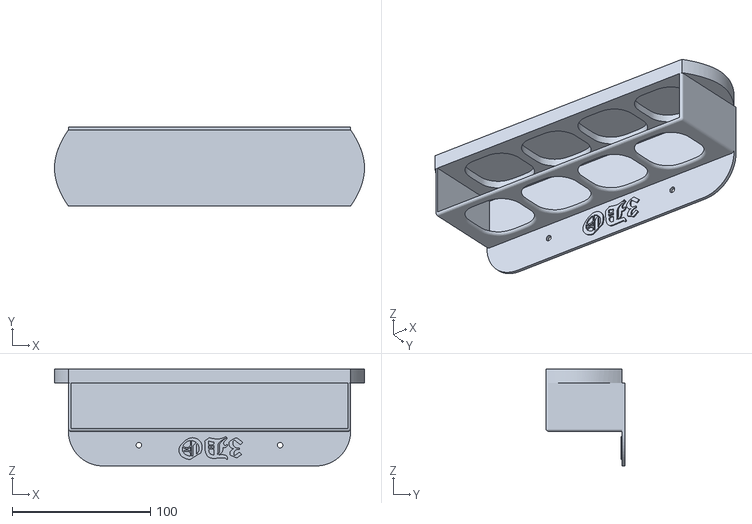
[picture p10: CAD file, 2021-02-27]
Desing-3D/3D/Soporte_Mandos_OLR.stl
224.0 x 57.2 x 70.0

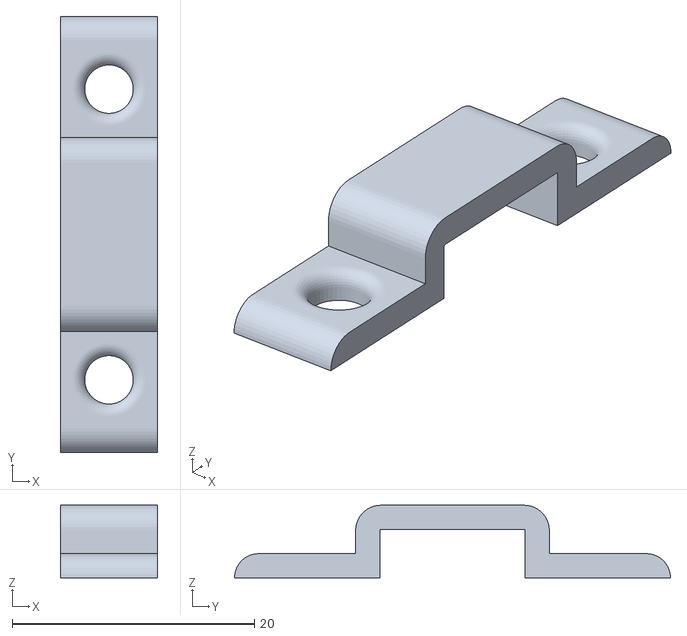
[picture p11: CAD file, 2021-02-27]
Desing-3D/3D/Sujeccion_Led.stl
8.00 x 36.0 x 6.00

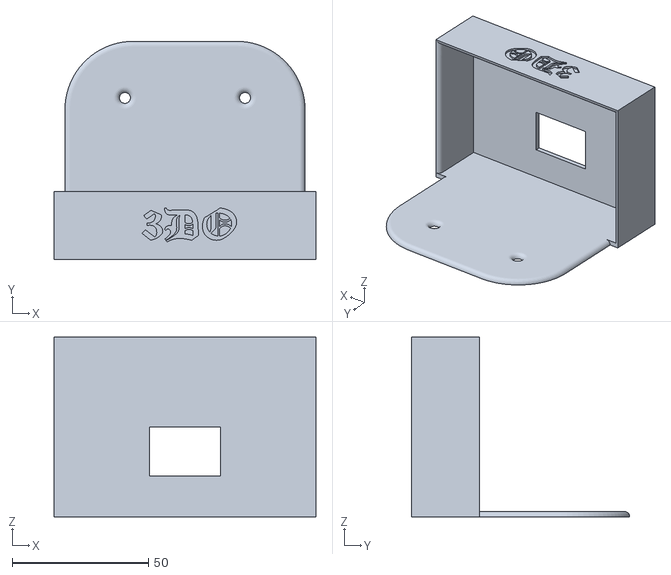
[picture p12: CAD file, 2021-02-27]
Desing-3D/3D/Soporte_Box_Control_OLR.stl
96.0 x 80.0 x 65.9

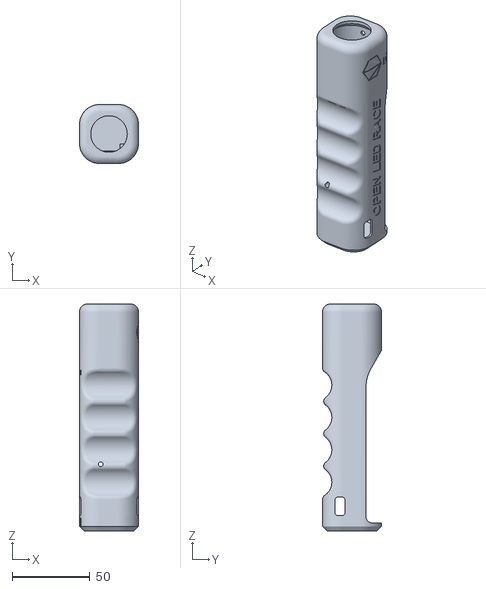
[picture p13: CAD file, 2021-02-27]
Desing-3D/3D/OLR_Mando_ESP32_Wemos_Bateria_Todo_en_1.stl
38.0 x 38.0 x 146.0

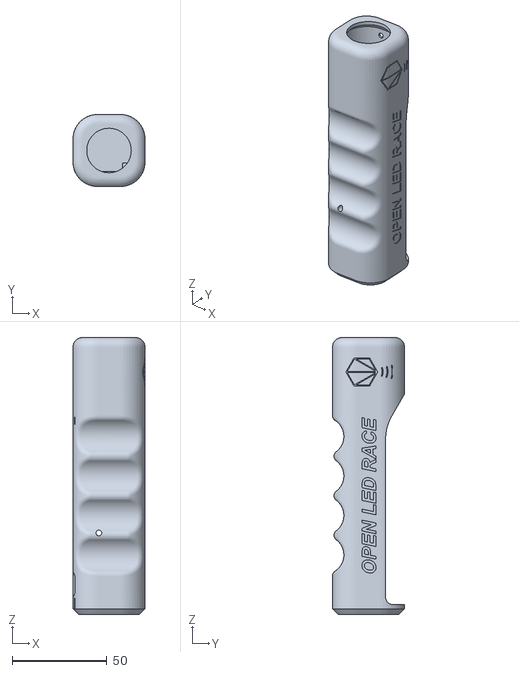
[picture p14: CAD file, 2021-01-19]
Desing-3D/3D/OLR_Mando_ESPNOW.stl
38.0 x 38.0 x 146.0

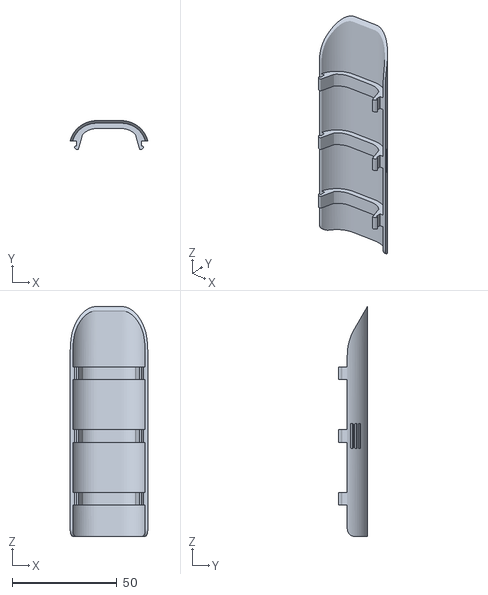
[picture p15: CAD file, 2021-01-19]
Desing-3D/3D/OLR_Mando-Tapa_ESPNOW.stl
37.1 x 13.7 x 109.8

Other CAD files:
Desing-3D/3D/OLR_Box_Control-Tapa-Gateway.stl
Desing-3D/3D/OLR_Box_Control-Gateway.stl

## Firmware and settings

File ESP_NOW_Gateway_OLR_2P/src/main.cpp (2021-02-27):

/*
  gurues@2021

  Gateway ESPNOW mandos Open Led Race 

  Basado en código de Rui Santos: https://RandomNerdTutorials.com/esp-now-many-to-one-esp8266-nodemcu/
  
*/

#include <Arduino.h>
#include <ESP8266WiFi.h>
#include <espnow.h>
#include <Adafruit_NeoPixel.h>

// Descomentar para realizar Degug por el puerto serie la parte de codigo ESP_NOW
#define DEBUG_Gateway_OLR
// Descomentar para realizar Degug por el puerto serie la parte de codigo Open Led Race
#define DEBUG_OLR

// Estructura de los datos a recibir
// Debe de ser la misma que el o los emisores
typedef struct struct_message {
    int player;
    bool pulso;
} struct_message;

// Estructura del mesaje recibido
struct_message myData;

//version Basic for PCB Rome Edition 
// 2 Player , without Boxes Track

#define WEMOS // Parte de código añadida por gurues para adaptarlo a WEMOS al código original Open Led Race

char const softwareId[] = "A2P0";  // A2P0: "A"=OpenLEDRace Team, "2P0"=Game ID (2P=2 Players, 0=Type 0 w slope w/ box)
char const version[] = "1.0.0";

#define MAXLED          300// MAX LEDs actives on strip

#ifdef WEMOS
  int PIN_P1 = 1;     
  int PIN_P2 = 1;
  #define PIN_LED        D1   // R 500 ohms to DI pin for WS2812 and WS2813, for WS2813 BI pin of first LED to GND  ,  CAP 1000 uF to VCC 5v/GND,power supplie 5V 2A  
  #define PIN_AUDIO      D2   // through CAP 2uf to speaker 8 ohms
  #define led            D4   // Led de control placa Wemos
#else
  #define PIN_P1         A2   // switch player 1 to PIN and GND
  #define PIN_P2         A0   // switch player 2 to PIN and GND 
  #define PIN_LED        2  // R 500 ohms to DI pin for WS2812 and WS2813, for WS2813 BI pin of first LED to GND  ,  CAP 1000 uF to VCC 5v/GND,power supplie 5V 2A  
  #define PIN_AUDIO      3   // through CAP 2uf to speaker 8 ohms
#endif

#define INI_RAMP 80
#define MED_RAMP 90
#define END_RAMP 100
#define HIGH_RAMP 16
bool ENABLE_RAMP=0;
bool VIEW_RAMP=0;

int NPIXELS=MAXLED; // leds on track
int cont_print=0;

#define COLOR1   Color(255,0,0)
#define COLOR2   Color(0,255,0)

#define COLOR1_tail   Color(i*3,0,0)
#define COLOR2_tail   Color(0,i*3,0)

// Serial Communications
#define EOL                 '\n' // End of Command char used in Protocol

#define REC_COMMAND_BUFLEN  32
char cmd[REC_COMMAND_BUFLEN];    // Stores command received by ReadSerialComand()

#define TX_COMMAND_BUFLEN  64
char txbuff[TX_COMMAND_BUFLEN];  // to prepare command strings to send 



// Callback funcion que se ejecuta cuando el dato es recibido
void OnDataRecv(uint8_t * mac_addr, uint8_t *incomingData, uint8_t len) {
  
  memcpy(&myData, incomingData, sizeof(myData));

  #ifdef DEBUG_Gateway_OLR
    char macStr[18];
    Serial.print("Packet received from: ");
    snprintf(macStr, sizeof(macStr), "%02x:%02x:%02x:%02x:%02x:%02x",
            mac_addr[0], mac_addr[1], mac_addr[2], mac_addr[3], mac_addr[4], mac_addr[5]);
    Serial.println(macStr);
    Serial.printf("Player ID %u: %u bytes\n", myData.player, len);
    Serial.printf("pulso value: %d \n", myData.pulso);
    Serial.println();
  #endif
  
  if (myData.player == 1){
    PIN_P1 = myData.pulso;
    digitalWrite (led,myData.pulso);
  }
  if (myData.player == 2){
    PIN_P2 = myData.pulso;
    digitalWrite (led, myData.pulso);
  }
 
}
 

int win_music[] = {
  2637, 2637, 0, 2637, 
  0, 2093, 2637, 0,
  3136    
};
      
byte  gravity_map[MAXLED];     

int TBEEP=0;
int FBEEP=0; 
byte SMOTOR=0;
float speed1=0;
float speed2=0;
float dist1=0;
float dist2=0;

byte loop1=0;
byte loop2=0;

byte leader=0;
byte loop_max=5; //total laps race


float ACEL=0.2;
float kf=0.015; //friction constant
float kg=0.003; //gravity constant

byte flag_sw1=0;
byte flag_sw2=0;
byte draworder=0;
 
unsigned long timestamp=0;

Adafruit_NeoPixel track = Adafruit_NeoPixel(MAXLED, PIN_LED, NEO_GRB + NEO_KHZ800);

int tdelay = 5; 

void set_ramp(byte H,byte a,byte b,byte c)
{for(int i=0;i<(b-a);i++){gravity_map[a+i]=127-i*((float)H/(b-a));};
 gravity_map[b]=127; 
 for(int i=0;i<(c-b);i++){gravity_map[b+i+1]=127+H-i*((float)H/(c-b));};
}

void set_loop(byte H,byte a,byte b,byte c)
{for(int i=0;i<(b-a);i++){gravity_map[a+i]=127-i*((float)H/(b-a));};
 gravity_map[b]=255; 
 for(int i=0;i<(c-b);i++){gravity_map[b+i+1]=127+H-i*((float)H/(c-b));};
}

// Command Send/Receive base functions 
///////////////////////////////////////

// vars used only in these functions
Stream*  _stream = &Serial;
int      _bufIdx;

/*
 *
 */
void sendSerialCommand(char* str) {
  // get command length
  int dlen=0;
  for(; dlen<TX_COMMAND_BUFLEN; dlen++ ) { 
    if(*(str+dlen) == EOL ) {
      dlen++; // send EOC 
      break;
    }
  }
  _stream->write(str, dlen);
  return;
}


/*
 * 
 */
void send_race_phase( int phase ) {
  sprintf(txbuff, "R%d%c",phase,EOL);
  sendSerialCommand(txbuff);
}


void start_race(){send_race_phase(4); // Race phase 4: Countdown 
                  for(int i=0;i<NPIXELS;i++){track.setPixelColor(i, track.Color(0,0,0));};
                  track.show();
                  delay(2000);
                  track.setPixelColor(12, track.Color(0,255,0));
                  track.setPixelColor(11, track.Color(0,255,0));
                  track.show();
                  tone(PIN_AUDIO,400);
                  delay(2000);
                  noTone(PIN_AUDIO);                  
                  track.setPixelColor(12, track.Color(0,0,0));
                  track.setPixelColor(11, track.Color(0,0,0));
                  track.setPixelColor(10, track.Color(255,255,0));
                  track.setPixelColor(9, track.Color(255,255,0));
                  track.show();
                  tone(PIN_AUDIO,600);
                  delay(2000);
                  noTone(PIN_AUDIO);                  
                  track.setPixelColor(9, track.Color(0,0,0));
                  track.setPixelColor(10, track.Color(0,0,0));
                  track.setPixelColor(8, track.Color(255,0,0));
                  track.setPixelColor(7, track.Color(255,0,0));
                  track.show();
                  tone(PIN_AUDIO,1200);
                  delay(2000);
                  noTone(PIN_AUDIO);                               
                  timestamp=0; 
                  send_race_phase(5); // Race phase 4: Race Started 
                 };

void winner_fx(byte w) {
               int msize = sizeof(win_music) / sizeof(int);
               for (int note = 0; note < msize; note++) {
               if (SMOTOR==1) {tone(PIN_AUDIO, win_music[note]/(3-w),200);} else {tone(PIN_AUDIO, win_music[note],200);};
               delay(230);
               noTone(PIN_AUDIO);}                                             
              };


int get_relative_position1( void ) {
    enum{
      MIN_RPOS = 0,
      MAX_RPOS = 99,
    };    
    int trackdist = 0;
    int pos = 0;  
    trackdist = (int)dist1 % NPIXELS;
    pos = map(trackdist, 0, NPIXELS -1, MIN_RPOS, MAX_RPOS);    
    return pos;
}

int get_relative_position2( void ) {
    enum{
      MIN_RPOS = 0,
      MAX_RPOS = 99,
    };    
    int trackdist = 0;
    int pos = 0;  
    trackdist = (int)dist2 % NPIXELS;
    pos = map(trackdist, 0, NPIXELS -1, MIN_RPOS, MAX_RPOS);    
    return pos;
}

void print_cars_position( void ) {
 int  rpos = get_relative_position1();
 sprintf( txbuff, "p%d%d%d,%d%c", 1, 1, loop1, rpos, EOL );
  sendSerialCommand(txbuff);
 
 rpos = get_relative_position2();
 sprintf( txbuff, "p%d%d%d,%d%c", 2, 1, loop2, rpos, EOL );
 sendSerialCommand(txbuff);
 
}

/*  Non blocking: call these function in main loop()
 *   
 *  If there are bytes available in Serial, READ JUST ONE char 
 *  and ADD it to the 'internal' cmd buffer 
 *    The char just read is an END OF COMMAND char ?
 *      N: Return 0 (no complete command available yet) 
 *      Y: Return buffer length (the caller will find the command in [buf]
 */
int checkSerial(char *   buf) { 
  while (_stream->available()) {
    if(_bufIdx < REC_COMMAND_BUFLEN - 2) {
      char data = _stream->read();
      if(data == EOL) {
        int cmsSize=_bufIdx;
        buf[_bufIdx++] = '\0';
        _bufIdx=0;
        return(cmsSize);
      } else {
        buf[_bufIdx++] = data;
      }
    } else {
      // buffer full 
      // reset and retunn error
      buf[_bufIdx++] = '\0';
      _bufIdx=0;
      return(-2); 
    }
  }
  return(0);
}




/*
 * 
 */

void checkSerialCommand(){
  
  int clen = checkSerial(cmd);
  if(clen == 0) return ;       // No commands received
  if(clen  < 0) {              // Error receiving command  
    sprintf( txbuff, "!1Error reading serial command:[%d]",clen); // Send a warning to host
    sendSerialCommand(txbuff);
    return;
  }
  // clen > 0 ---> Command with length=clen ready in  cmd[]

  switch (cmd[0]) {
    case '#':                         // Handshake -> send back 
      {
        sprintf( txbuff, "#%c", EOL );
        sendSerialCommand(txbuff);    
      }
      return;

  case  '@' :                         // Enter "Configuration Mode"
    {
      // send back @OK 
      // No real cfg mode here, but send @OK so the Desktop app (Upload, configure)
      // can send a GET SOFTWARE Type/Ver command and identify this software
        sprintf( txbuff, "@OK%c", EOL );
        sendSerialCommand(txbuff);          
    }
    return;
    
  case '?' :                          // Get Software Id
    {
      sprintf( txbuff, "%s%s%c", "?", softwareId, EOL );
      sendSerialCommand(txbuff);    
    }
    return;
  
  case '%' :                          // Get Software Version
    {
      sprintf( txbuff, "%s%s%c", "%", version, EOL );
      sendSerialCommand(txbuff);    
    }
    return;    
  } 

  // if we get here, the command it's not managed by this software -> Answer <CommandId>NOK
  sprintf(txbuff, "%cNOK%c", cmd[0], EOL );  
  sendSerialCommand(txbuff);
  
  return; 
}


void burning1(){
//to do
 }

void burning2(){
//to do
 }

void track_rain_fx(){
//to do
 }

void track_oil_fx(){
//to do
 }

void track_snow_fx(){
//to do
 }


void fuel_empty(){
//to do
 }

void fill_fuel_fx(){
//to do
 }

void in_track_boxs_fx(){
//to do
 }

void pause_track_boxs_fx(){
//to do
 }
 
void flag_boxs_stop(){
//to do
 }

void flag_boxs_ready(){
//to do
 }

void draw_safety_car(){
//to do
 }

void telemetry_rx(){
  //to do
 }
 
void telemetry_tx(){
  //to do
 }

void telemetry_lap_time_car1(){
//to do
 }

void telemetry_lap_time_car2(){
//to do
 }

void telemetry_record_lap(){
//to do
 }

void telemetry_total_time(){
//to do
 }

int read_sensor(byte player){
  return(0); //to do
}

int calibration_sensor(byte player){
  return(0); //to do
}

int display_lcd_laps(){
    return(0); //to do  
}

int display_lcd_time(){
    return(0); //to do  
}

void draw_car1(void){for(int i=0;i<=loop1;i++){track.setPixelColor(((word)dist1 % NPIXELS)+i, track.COLOR1);};                   
 }

void draw_car2(void){for(int i=0;i<=loop2;i++){track.setPixelColor(((word)dist2 % NPIXELS)+i, track.COLOR2);};            
 }


//**************************************************************************************************************************************

void setup() {

  //#ifdef DEBUG_Gateway_OLR
    Serial.begin(115200);
  //#endif

  pinMode (led, OUTPUT);
  digitalWrite (led, HIGH);

  // Configura el dispositivo como Wi-Fi Station
  WiFi.mode(WIFI_STA);
  WiFi.disconnect();

  // Inicia protocolo ESP-NOW
  if (esp_now_init() != 0) {
    #ifdef DEBUG_Gateway_OLR
      Serial.println("Error inicializando ESP-NOW");
    #endif
    return;
  }
 
  // Se configura el disòsitivo como Receptor
  esp_now_set_self_role(ESP_NOW_ROLE_SLAVE);
  // Se registra callback de recepción de mensajes
  esp_now_register_recv_cb(OnDataRecv);

  #ifdef DEBUG_Gateway_OLR
    Serial.println(" ");
    Serial.println("INICIALIZADO GATEWAY ESPNOW OPEN LED RACE");
  #endif

  for(int i=0;i<NPIXELS;i++){gravity_map[i]=127;};
  track.begin(); 
  #ifdef WEMOS
    if (PIN_P1==0) //push switch 1 on reset for activate physics
  #else
    pinMode(PIN_P1,INPUT_PULLUP); 
    pinMode(PIN_P2,INPUT_PULLUP);  
  if ((digitalRead(PIN_P1)==0)) //push switch 1 on reset for activate physics
  #endif
  {ENABLE_RAMP=1;
   set_ramp(HIGH_RAMP,INI_RAMP,MED_RAMP,END_RAMP); 
   for(int i=0;i<(MED_RAMP-INI_RAMP);i++){track.setPixelColor(INI_RAMP+i, track.Color(24+i*4,0,24+i*4) );};  
   for(int i=0;i<(END_RAMP-MED_RAMP);i++){track.setPixelColor(END_RAMP-i, track.Color(24+i*4,0,24+i*4) );};                                           
   track.show();
   delay(1000);
   tone(PIN_AUDIO,500);delay(500);noTone(PIN_AUDIO);delay(500);
  #ifdef WEMOS
    if (PIN_P1==0) //push switch 1 on reset for activate physics
  #else
    if ((digitalRead(PIN_P1)==0))
  #endif 
    {VIEW_RAMP=1;} // if retain push switch 1 set view ramp
   else {for(int i=0;i<NPIXELS;i++){track.setPixelColor(i, track.Color(0,0,0));};
         track.show();
         VIEW_RAMP=0;  
        }; 
   
  };
  #ifdef WEMOS
    if (((PIN_P2)==0)) {delay(1000); tone(PIN_AUDIO,1000);delay(500);noTone(PIN_AUDIO);delay(500);if (((PIN_P2)==1)) SMOTOR=1;} //push switch 2 until a tone beep on reset for activate magic FX  ;-)
  #else
    if ((digitalRead(PIN_P2)==0)) {delay(1000); tone(PIN_AUDIO,1000);delay(500);noTone(PIN_AUDIO);delay(500);if ((digitalRead(PIN_P2)==1)) SMOTOR=1;} //push switch 2 until a tone beep on reset for activate magic FX  ;-)
  #endif
  start_race();

}

void loop() {   

    // look for commands received on serial 
    checkSerialCommand();

  
    for(int i=0;i<NPIXELS;i++){track.setPixelColor(i, track.Color(0,0,0));};
    if ((ENABLE_RAMP==1) && ( VIEW_RAMP==1)) {for(int i=0;i<(MED_RAMP-INI_RAMP);i++){track.setPixelColor(INI_RAMP+i, track.Color(24+i*4,0,24+i*4) );};  
                                              for(int i=0;i<(END_RAMP-MED_RAMP);i++){track.setPixelColor(END_RAMP-i, track.Color(24+i*4,0,24+i*4) );};                                           
                                             };    
    #ifdef WEMOS
      if ( (flag_sw1==1) && ((PIN_P1)==0) ) {flag_sw1=0;speed1+=ACEL;};
      if ( (flag_sw1==0) && ((PIN_P1)==1) ) {flag_sw1=1;};
    #else
      if ( (flag_sw1==1) && (digitalRead(PIN_P1)==0) ) {flag_sw1=0;speed1+=ACEL;};
      if ( (flag_sw1==0) && (digitalRead(PIN_P1)==1) ) {flag_sw1=1;};
    #endif
    if ((gravity_map[(word)dist1 % NPIXELS])<127) speed1-=kg*(127-(gravity_map[(word)dist1 % NPIXELS]));
    if ((gravity_map[(word)dist1 % NPIXELS])>127) speed1+=kg*((gravity_map[(word)dist1 % NPIXELS])-127);
        
    speed1-=speed1*kf; 
    #ifdef WEMOS
      if ( (flag_sw2==1) && ((PIN_P2)==0) ) {flag_sw2=0;speed2+=ACEL;};
      if ( (flag_sw2==0) && ((PIN_P2)==1) ) {flag_sw2=1;};
    #else
      if ( (flag_sw2==1) && (digitalRead(PIN_P2)==0) ) {flag_sw2=0;speed2+=ACEL;};
      if ( (flag_sw2==0) && (digitalRead(PIN_P2)==1) ) {flag_sw2=1;};
    #endif
    if ((gravity_map[(word)dist2 % NPIXELS])<127) speed2-=kg*(127-(gravity_map[(word)dist2 % NPIXELS]));
    if ((gravity_map[(word)dist2 % NPIXELS])>127) speed2+=kg*((gravity_map[(word)dist2 % NPIXELS])-127);
        
    speed2-=speed2*kf; 
        
    dist1+=speed1;
    dist2+=speed2;

    if (dist1>dist2) {if (leader==2) {FBEEP=440;TBEEP=10;}
                      leader=1;} 
    if (dist2>dist1) {if (leader==1) {FBEEP=440*2;TBEEP=10;}
                      leader=2;};

    
      
    if (dist1>NPIXELS*loop1) {loop1++;TBEEP=10;FBEEP=440;};
    if (dist2>NPIXELS*loop2) {loop2++;TBEEP=10;FBEEP=440*2;};

    if (loop1>loop_max) {sprintf( txbuff, "w1%c", EOL );
                         sendSerialCommand(txbuff); // Send Winner=1 command
                         for(int i=0;i<NPIXELS/10;i++){track.setPixelColor(i,track.COLOR1_tail);}; track.show();
                         winner_fx(1);loop1=0;loop2=0;dist1=0;dist2=0;speed1=0;speed2=0;timestamp=0;
                         start_race();
                        }
    if (loop2>loop_max) {sprintf( txbuff, "w2%c", EOL );
                         sendSerialCommand(txbuff); // Send Winner=2 command
                         for(int i=0;i<NPIXELS/10;i++){track.setPixelColor(i, track.COLOR2_tail);}; track.show();
                         winner_fx(2);loop1=0;loop2=0;dist1=0;dist2=0;speed1=0;speed2=0;timestamp=0;
                         start_race();
                        }
   
     if ((millis() & 512)==(512*draworder)) {if (draworder==0) {draworder=1;}
                          else {draworder=0;}
                         };
    if (abs(round(speed1*100))>abs(round(speed2*100))) {draworder=1;};
    if (abs(round(speed2*100))>abs(round(speed1*100))) {draworder=0;};
       
    if ( draworder==0 ) {
      draw_car1();
      draw_car2();
    }
    else {
      draw_car2();
      draw_car1();
    } 
                 
    track.show(); 
    if (SMOTOR==1) tone(PIN_AUDIO,FBEEP+int(speed1*440*2)+int(speed2*440*3));
    delay(tdelay);
    if (TBEEP>0) {TBEEP--;} else {FBEEP=0;};
    cont_print++; 
    if (cont_print>100) {print_cars_position();cont_print=0;}
         
}

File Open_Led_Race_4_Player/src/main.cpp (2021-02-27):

/*
 * ____                     _      ______ _____    _____
  / __ \                   | |    |  ____|  __ \  |  __ \
 | |  | |_ __   ___ _ __   | |    | |__  | |  | | | |__) |__ _  ___ ___
 | |  | | '_ \ / _ \ '_ \  | |    |  __| | |  | | |  _  // _` |/ __/ _ \
 | |__| | |_) |  __/ | | | | |____| |____| |__| | | | \ \ (_| | (_|  __/
  \____/| .__/ \___|_| |_| |______|______|_____/  |_|  \_\__,_|\___\___|
        | |
        |_|
 Open LED Race
 An minimalist cars race for LED strip

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

 First public version by:
    Angel Maldonado (https://gitlab.com/angeljmc) 
    Gerardo Barbarov (gbarbarov AT singulardevices DOT com)  

  Basen on original idea and 2 players code by: 
    Gerardo Barbarov  for Arduino day Seville 2019
    https://github.com/gbarbarov/led-race

    
 Public Repository for this code:
   https://gitlab.com/open-led-race/olr-arduino

*/

 
// 2020/12/10 - Ver 0.9.6
//   --see changelog.txt

char const softwareId[] = "A4P0";  // A4P -> A = Open LED Race, 4P0 = Game ID (4P = 4 Players, 0=Type 0)
char const version[] = "0.9.6";


#include <Arduino.h>
#include <Adafruit_NeoPixel.h>
#include <EEPROM.h>
#include "olr-lib.h"
#include "olr-param.h"
#include "SoftTimer.h"
#include "SerialCommand.h"

#define PIN_LED        2    // R 500 ohms to DI pin for WS2812 and WS2813, for WS2813 BI pin of first LED to GND  ,  CAP 1000 uF to VCC 5v/GND,power supplie 5V 2A
#define PIN_AUDIO      3    // through CAP 2uf to speaker 8 ohms

#define REC_COMMAND_BUFLEN 32
#define EOL            '\n' // End of Command char used in Protocol

#define COLOR1         track.Color(255,0,0)
#define COLOR2         track.Color(0,255,0)
#define COLOR3         track.Color(0,0,255)
#define COLOR4         track.Color(255,255,255)

#define COLOR_RAMP     track.Color(64,0,64)
#define COLOR_COIN     track.Color(0,255,255)
#define COLOR_BOXMARKS track.Color(64,64,0)
#define LED_SEMAPHORE  12 

#define CONTDOWN_PHASE_DURATION  2000 
#define CONTDOWN_STARTSOUND_DURATION  40 

#define NEWRACE_DELAY  5000 

enum{
  MAX_CARS = 4,
};


enum loglevel {  // used in Serial Protocol "!" command (send log/error messageS)
    ECHO = 0,
    DISABLE = 0,
    LOG = 1,
    WARNING = 2,
    ERROR = 3
};


enum resp{
  NOK   = -1,
  NOTHING = 0,
  OK      = 1
};

typedef struct ack{
  enum resp rp;
  char type;
}ack_t;



struct cfgcircuit{
    int outtunnel;
};

enum phases{
    IDLE = 0,
    CONFIG,
    CONFIG_OK,
    READY,
    COUNTDOWN,
    RACING,
    PAUSE,
    RESUME,
    COMPLETE,
    RACE_PHASES
};

struct race{
    struct cfgrace    cfg;
    struct cfgcircuit circ;
    bool              newcfg;
    enum phases       phase;
    byte              numcars;
    int               winner; 
};


byte SMOTOR=0;
int TBEEP=0;
int FBEEP=0;

/*------------------------------------------------------*/
enum loglevel verbose = DISABLE;

static struct race race;
static car_t cars[ MAX_CARS ];
static controller_t switchs[ MAX_CARS ];
static track_t tck;

static int const eeadrInfo = 0; 

char txbuff[64];




static unsigned long lastmillis = 0;

SoftTimer customDelay = SoftTimer(); // non blocking delay()

// Used to manage countdown phases
int     countdown_phase=1;
bool    countdown_new_phase=true;


int win_music[] = {
  2637, 2637, 0, 2637,
  0, 2093, 2637, 0,
  3136
};

//int TBEEP=3;

char tracksID[ NUM_TRACKS ][2] ={"U","M","B","I","O"};

/*  ----------- Function prototypes ------------------- */

void sendResponse( ack_t *ack);

ack_t manageSerialCommand();

void printdebug( const char * msg, int errlevel );
void print_cars_positions( car_t* cars);
void run_racecycle( void );
void draw_winner( track_t* tck, uint32_t color);


char cmd[REC_COMMAND_BUFLEN]; // Stores command received by ReadSerialComand()
SerialCommand serialCommand = SerialCommand(cmd, REC_COMMAND_BUFLEN, EOL, &Serial); // get complete command from serial

Adafruit_NeoPixel track;



void send_phase( int phase ) {
  sprintf(txbuff, "R%d%c",phase,EOL);
  serialCommand.sendCommand(txbuff);
}

void draw_car( track_t* tck, car_t* car ) {
    struct cfgtrack const* cfg = &tck->cfg.track;
    
    switch ( car->trackID ){
      case TRACK_MAIN:
        for(int i=0; i<= car->nlap; ++i )
          track.setPixelColor( ((word)car->dist % cfg->nled_main) + i, car->color );
      break;
      case TRACK_AUX:
        for(int i=0; i<= car->nlap; ++i )     
          track.setPixelColor( (word)(cfg->nled_main + cfg->nled_aux - car->dist_aux) + i, car->color);         
      break;
    }
}

void run_racecycle( car_t *car, int i ) {
    struct cfgtrack const* cfg = &tck.cfg.track;
    
    if( car->st == CAR_ENTER ) {
        car_resetPosition( car );
        if( car->repeats < race.cfg.nrepeat )
          car->st = CAR_RACING;
        else
          car->st = CAR_GO_OUT;
    }
    
    if( car->st == CAR_RACING ) {
        update_track( &tck, car );
        car_updateController( car );
        draw_car( &tck, car );

        if( car->nlap == race.cfg.nlap 
              && !car->leaving
              && car->dist > ( cfg->nled_main*car->nlap - race.circ.outtunnel ) ) {
            car->leaving = true;
            car->st = CAR_LEAVING;
        }

        if( car->nlap > race.cfg.nlap ) {
            ++car->repeats;
            car->st = CAR_GO_OUT;
        }

        if( car->repeats >= race.cfg.nrepeat 
              && race.cfg.finishline ) {
            car->st = CAR_FINISH;  
        }
    }

    if ( car->st == CAR_FINISH ){
        car->trackID = NOT_TRACK;
        sprintf( txbuff, "w%d%c", i + 1, EOL );
        serialCommand.sendCommand(txbuff);
        //sendCommand(txbuff);

        car_resetPosition( car );
    }
}


int get_relative_position( car_t* car ) {
    enum{
      MIN_RPOS = 0,
      MAX_RPOS = 99,
    };
    struct cfgtrack const* cfg = &tck.cfg.track;
    int trackdist = 0;
    int pos = 0;

    switch ( car->trackID ){
      case TRACK_MAIN:
        trackdist = (int)car->dist % cfg->nled_main;
        pos = map(trackdist, 0, cfg->nled_main -1, MIN_RPOS, MAX_RPOS);
      break;
      case TRACK_AUX:
        trackdist = (int)car->dist_aux;
        pos = map(trackdist, 0, cfg->nled_aux -1, MIN_RPOS, MAX_RPOS);
      break;
    }
    return pos;
}


void print_cars_positions( car_t* cars ) {
    
    bool outallcar = true;
    for( int i = 0; i < race.numcars; ++i)
      outallcar &= cars[i].st == CAR_WAITING;
    
    if ( outallcar ) return;
    
    for( int i = 0; i < race.numcars; ++i ) {
      int const rpos = get_relative_position( &cars[i] );
      sprintf( txbuff, "p%d%s%d,%d%c", i + 1, tracksID[cars[i].trackID], cars[i].nlap, rpos, EOL );
      serialCommand.sendCommand(txbuff);
      //sendCommand(txbuff);
    }
}

void strip_clear( track_t* tck ) {
    struct cfgtrack const* cfg = &tck->cfg.track;
    for( int i=0; i < cfg->nled_main; i++)
        track.setPixelColor( i, track.Color(0,0,0) );

    for( int i=0; i < cfg->nled_aux; i++)
        track.setPixelColor( cfg->nled_main+i, track.Color(0,0,0) );
}
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

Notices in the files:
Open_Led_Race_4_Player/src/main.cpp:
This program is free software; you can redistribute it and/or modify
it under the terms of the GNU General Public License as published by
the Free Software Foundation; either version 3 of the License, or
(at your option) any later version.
